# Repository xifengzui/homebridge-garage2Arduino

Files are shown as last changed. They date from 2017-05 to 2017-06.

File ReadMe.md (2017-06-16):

## Arduino Garage Controller base on homebridge 

This project is based on [homebridge](https://github.com/nfarina/homebridge)

this project is a  complete project which aim to use siri to control my  garage.

**It contains**  

**Homebridge plug-ins**: garage controller plugins.

**Sch Pcb** :mother board for DCDC Power module,Arduino Nano V3,ESP8266 wifi module,OLED Screen,Relay module,Rotray Encoder and 3 touch button.(Altium Designer 14.1)

**Model**:   bracket (Sketchup Pro 2015)

Read More: http://www.arkis.me

本项目包含一个完整使用siri控制车库的所有内容。

包含了以下内容

Homebridge插件:转接homebridge命令为socket通讯，控制车库控制器

电路原理图及制版图:主板，用于支持220V转5V电源，3v3电源，Arduino Nano V3,ESP8266无线模块，

OLED屏幕，继电器，旋转编码器及3个触摸按钮

3d模型:可用于3D打印的外壳模型。

具体说明请查看 http://www.arkis.me

**Working Flow**

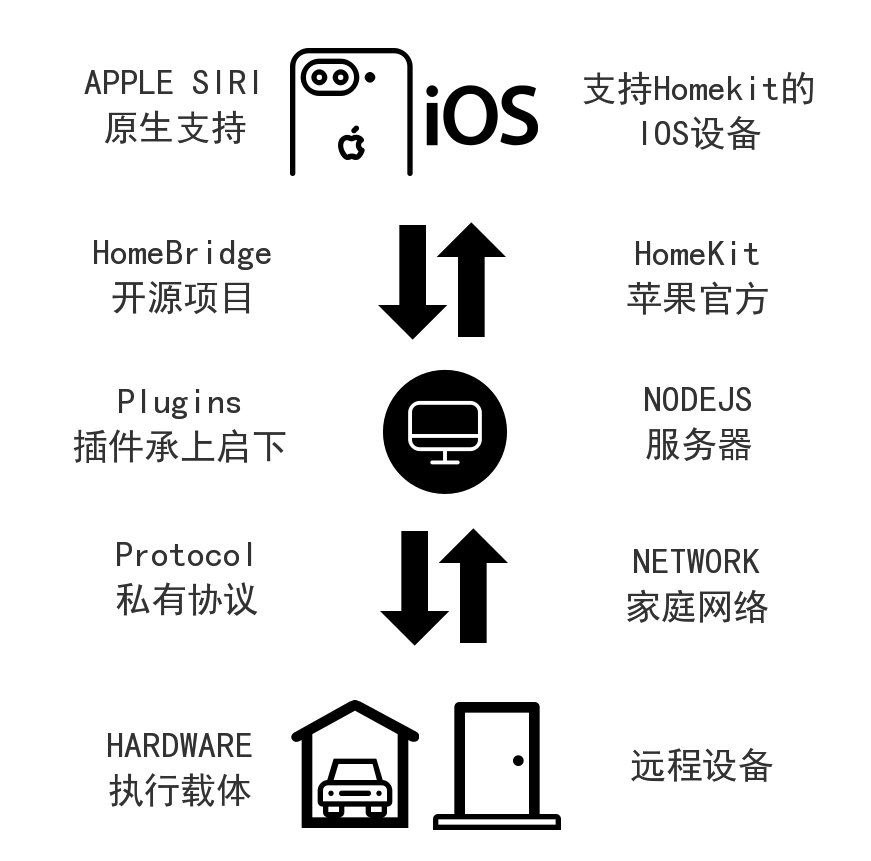
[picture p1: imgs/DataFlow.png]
dataflow


**Network Topology**

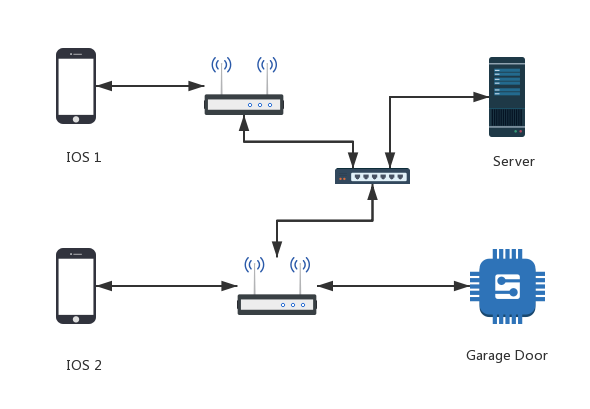
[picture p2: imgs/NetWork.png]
network topology


**Hardware**

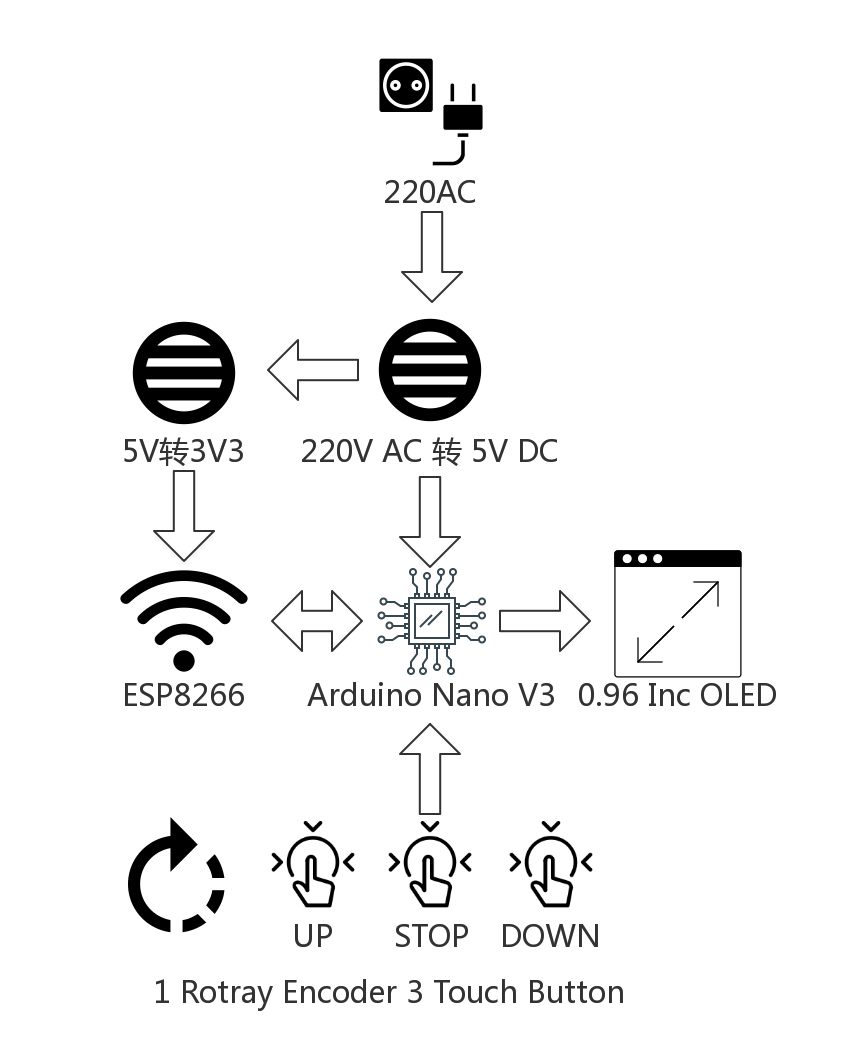
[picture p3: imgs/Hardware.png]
hardware


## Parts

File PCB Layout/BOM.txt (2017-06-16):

名称						价格	数量	用途	TB地址	备注
ESP8266串口WIFI无线模块WIF收发无线模块		9.4	1	数据收发	https://detail.tmall.com/item.htm?id=540067174120&spm=a1z09.2.0.0.xazHRp&_u=v96l7ape468
Arduino Nano V3 ATMega328P			9.2	1	主控	https://item.taobao.com/item.htm?spm=a1z09.2.0.0.xazHRp&id=531487412230&_u=v96l7apf7c1	
4路带继电器光耦模块				6.59	1	电机控制	https://item.taobao.com/item.htm?spm=a1z09.2.0.0.xazHRp&id=6731653313&_u=v96l7ap744f	
220V转5V电源模块				10.5	1	总电源	https://buyertrade.taobao.com/trade/itemlist/list_bought_items.htm?spm=a21bo.50862.1997525045.2.RBEhap	
电源3脚插座					5	1	电源头	https://item.taobao.com/item.htm?spm=a1z09.2.0.0.xazHRp&id=520812099558&_u=v96l7apd51a
电源3脚插母					4.5	1	电源母头	https://item.taobao.com/item.htm?spm=a1z09.2.0.0.xazHRp&id=523912847491&_u=v96l7ap084a	
触摸按钮					2.6	3	按钮	https://detail.tmall.com/item.htm?id=524832982387&spm=a1z09.2.0.0.xazHRp&_u=v96l7ap4716	按钮功能
旋转编码器					5	1	旋钮	https://buyertrade.taobao.com/trade/itemlist/list_bought_items.htm?spm=a21bo.50862.1997525045.2.RBEhap	旋钮
5V转3.3V DCDC电源模块				4	1	3v3电源	https://item.taobao.com/item.htm?spm=a1z09.2.0.0.xazHRp&id=534263863865&_u=v96l7ap15f1	给ESP8266供电
6pin排线					0.6	1	排线	https://item.taobao.com/item.htm?spm=a1z09.2.0.0.xazHRp&id=542126237591&_u=v96l7ap46ef	连接继电器模块的
M3螺丝若干	 	 	 	
OLED Screen                                     14.8    1       显示屏  https://item.taobao.com/item.htm?spm=a1z09.2.0.0.3NjgBQ&id=40854288700&_u=g96l7ap0f8b	 	 
总价	57.3

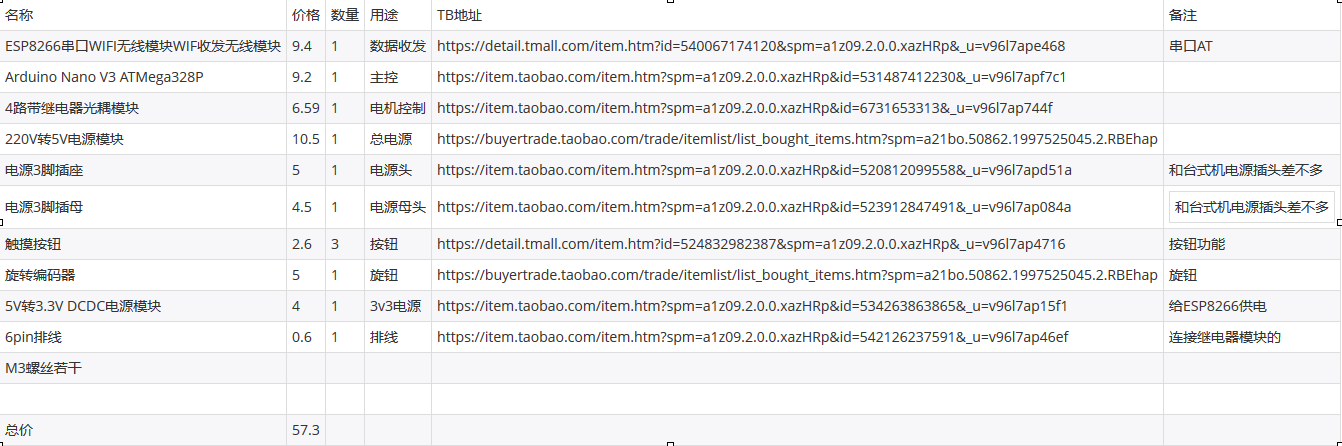
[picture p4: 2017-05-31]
PCB Layout/BOM.png

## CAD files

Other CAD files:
3D Model/box Left.skp
3D Model/box Right.skp
3D Model/box.skp

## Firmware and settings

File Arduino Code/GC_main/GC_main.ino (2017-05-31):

/*****************************************************************************
* File    : GC_main.ino
* Author  : 惜枫醉
* Date    : 2017/04/06
* Brief   : 车库控制器主程序
*
* Copyright (c) 2000-2020 惜枫醉 All Rights Reserved.
* Remarks :修改日志
******************************************************************************/


/*****************************************************************************
*                               头文件引用
******************************************************************************/
//arduino头文件都要包在主文件里，还是比较奇怪的,还有 所有函数都不需要预先声明，但C++部分又是要声明的。
#include <MsTimer2.h>
#include <avr/pgmspace.h>
#include <EEPROM.h>
//#include <Wire.h>
#include "GC_eeprom.h"
#include "GC_def.h"
#include "GC_key.h"
#include "GC_relay.h"
#include "GC_timer.h"
#include "GC_oled.h"
#include "GC_oledFont.h"
#include "GC_menu.h"
#include "GC_wifi.h"
/*****************************************************************************
*                                常量定义
******************************************************************************/


/*****************************************************************************
*                                 宏定义
******************************************************************************/
#define DMSG
#ifdef DMSG
    #define dbgMsg(x) do{\
        char *dbgStr = PSTR(x);\
        while(pgm_read_byte(dbgStr) != NULL)\
        {\
            Serial.write(pgm_read_byte(dbgStr));\
            dbgStr++;\
        }\
        Serial.write('\n');\
    }while(0)
        
#else
    #define dbgMsg(x) 
#endif

/*****************************************************************************
*                              数据类型定义
******************************************************************************/


/*****************************************************************************
*                                函数声明
******************************************************************************/


/*****************************************************************************
*                                变量定义
******************************************************************************/

void setup()
{
    int ret = NULL;
    Serial.begin(9600);
    EEPROM_init();
    TIMER_init();
    OLED_init();
    KEY_init();
	RELAY_init();
    delay(1000);
    WIFI_init();
    APP_menuGen();//生成菜单，如果对菜单逻辑有疑问，可以参考此代码
    
    
}   

void loop() 
{
    APP_menuLogic();
    APP_backgroundService();
    APP_timerServiceBody();
}

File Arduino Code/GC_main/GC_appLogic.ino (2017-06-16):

/*****************************************************************************
* File    : GC_appLogic.ino
* Author  : 惜枫醉
* Date    : 2017/04/09
* Brief   : 车库控制的总逻辑 
*
* Copyright (c) 2000-2020 惜枫醉 All Rights Reserved.
* Remarks :修改日志
******************************************************************************/


/*****************************************************************************
*                               头文件引用
******************************************************************************/


/*****************************************************************************
*                                常量定义
******************************************************************************/


/*****************************************************************************
*                                 宏定义
******************************************************************************/
#define TEXT_ALIGN_LEFT     0
#define TEXT_ALIGN_MIDDLE   1
#define TEXT_ALIGN_RIGHT    2

#define GARAGE_TIME_UP      0
#define GARAGE_TIME_DOWN    1

#define WIFI_MAX_NAME_LEN 16
#define WIFI_MAX_PASSWD_LEN 16


#define STAT_SELECT_CHAR 0
#define STAT_EDIT_CHAR 1
#define STAT_STRLEN_CHANGE 2



#define STAT_HK_CLOSED  0   //已关闭
#define STAT_HK_CLOSING 1   //关闭中
#define STAT_HK_CLOSE   2   //请求关闭

#define STAT_HK_OPENED  3   //已打开
#define STAT_HK_OPENING 4   //打开中
#define STAT_HK_OPEN    5   //请求打开

#define STAT_HK_IDEL 6
#define STAT_HK_BUSY 7

/*****************************************************************************
*                              数据类型定义
******************************************************************************/
struct APP_GarageParms
{
    Uint8 upTime;
    Uint8 *upTimeStr;
    Uint8 downTime;
    Uint8 *downTimeStr;
    volatile Uint8 isEnableHomeKit;
    volatile Uint8 status;
};

struct APP_WifiParms
{
    Uint8 isConnected;
    Uint8 *ssid;
    Uint8 ssidLen;
    Uint8 *password;
    Uint8 passwordLen;
    Uint8 *srvIp;
    Uint8 devId;
};


struct APP_serviceParms
{
    Uint8 *wifiStatus;
};

/*****************************************************************************
*                                函数声明
******************************************************************************/


/*****************************************************************************
*                                变量定义
******************************************************************************/


//主页菜单项  
static MENU_Handle      gMainMenu = NULL; 
static MENU_ItemHandle  gMainMenu_garage = NULL;
static MENU_ItemHandle  gMainMenu_wifi = NULL;

//车库菜单项
static MENU_Handle      gGarageMenu = NULL;
static MENU_ItemHandle  gGarageMenu_goBack = NULL;
static MENU_ItemHandle  gGarageMenu_upTimeMenu = NULL;
static MENU_ItemHandle  gGarageMenu_downTimeMenu = NULL;
static MENU_ItemHandle  gGarageMenu_enableHomekit = NULL;
static MENU_ItemHandle  gGarageMenu_disableHomekit = NULL;

//wifi菜单项
static MENU_Handle      gWifiMenu = NULL;
static MENU_ItemHandle  gWifiMenu_goBack = NULL;
static MENU_ItemHandle  gWifiMenu_ssid = NULL;
static MENU_ItemHandle  gWifiMenu_password = NULL;
static MENU_ItemHandle  gWifiMenu_connect = NULL;
static MENU_ItemHandle  gWifiMenu_srvIp = NULL;
static MENU_ItemHandle  gWifiMenu_devId = NULL;

//索引句柄，整个菜单的渲染逻辑通过索引句柄来进行的
static MENU_Handle *posHandle = NULL;
static MENU_ItemHandle *posItemHandle = NULL;

//服务器IP地址,设备会向这个ip上报车库门的状态 
static Uint8            gSrv_ip[4] = {192,168,1,200};

//车库门上和下的时间设置
static Uint8            gGarageMenu_downTimeDispMem[] =    "DOWN TIME: 15";
static Uint8            gGarageMenu_upTimeDispMem[]   =    "UP   TIME: 15";

//wifi字符串的内存
static Uint8            gWifiMenu_wifiNameMem[WIFI_MAX_NAME_LEN+1] = "";
static Uint8            gWifiMenu_passwordMem[WIFI_MAX_PASSWD_LEN+1] = "";


static volatile Uint8 gTimerDaemonFlag = 0;//由于定时器中断不建议做很多事情，所以用标志位，让她在主函数运行


static volatile Uint16 gClock = 0; //用于整个设备的计数时间戳

struct APP_GarageParms gAPP_garagePrms = 
{
    .upTime = 0,
    .upTimeStr = gGarageMenu_upTimeDispMem,
    .downTime = 0,
    .downTimeStr = gGarageMenu_downTimeDispMem,
    .isEnableHomeKit = 0,
    .status = STAT_HK_IDEL
};

struct APP_WifiParms gApp_wifiPrms = 
{
    .isConnected = 0,
    .ssid = gWifiMenu_wifiNameMem,
    .ssidLen = 4,
    .password = gWifiMenu_passwordMem,
    .passwordLen = 8,
    .srvIp = gSrv_ip,
    .devId = 66
};


/*****************************************************************************
* Author  : 惜枫醉
* Date    : 2017/05/28
* Brief   : 从eeprom获取掉电的数据
* Return  : 
* Remarks : 
******************************************************************************/
Uint8 APP_dumpPrms(void)
{
    gAPP_garagePrms.upTime =  EEPROM_restore(EEPROM_UPTIME);
    gAPP_garagePrms.downTime =  EEPROM_restore(EEPROM_DOWNTIME);
    gApp_wifiPrms.srvIp[0] = EEPROM_restore(EEPROM_SRVIPSEG0);
    gApp_wifiPrms.srvIp[1] = EEPROM_restore(EEPROM_SRVIPSEG1);
    gApp_wifiPrms.srvIp[2] = EEPROM_restore(EEPROM_SRVIPSEG2);
    gApp_wifiPrms.srvIp[3] = EEPROM_restore(EEPROM_SRVIPSEG3);
    gApp_wifiPrms.devId = EEPROM_restore(EEPROM_DEVID);
    gAPP_garagePrms.isEnableHomeKit = EEPROM_restore(EEPROM_ISENHOMEKIT);
}
/*****************************************************************************
* Author  : 惜枫醉
* Date    : 2017/05/28
* Brief   : 将数据刷入eeprom
* Return  : 
* Remarks : 
******************************************************************************/
Uint8 APP_flushPrms(void)
{
    if(gAPP_garagePrms.upTime !=  EEPROM_restore(EEPROM_UPTIME))
    {
        EEPROM_store(EEPROM_UPTIME, gAPP_garagePrms.upTime);
    }
    
    if(gAPP_garagePrms.downTime !=  EEPROM_restore(EEPROM_DOWNTIME))
    {
        EEPROM_store(EEPROM_DOWNTIME, gAPP_garagePrms.downTime);
    }

    if(gApp_wifiPrms.srvIp[0] !=  EEPROM_restore(EEPROM_SRVIPSEG0))
    {
        EEPROM_store(EEPROM_SRVIPSEG0, gApp_wifiPrms.srvIp[0]);
    }

    if(gApp_wifiPrms.srvIp[1] !=  EEPROM_restore(EEPROM_SRVIPSEG1))
    {
        EEPROM_store(EEPROM_SRVIPSEG1, gApp_wifiPrms.srvIp[1]);
    }

    if(gApp_wifiPrms.srvIp[2] !=  EEPROM_restore(EEPROM_SRVIPSEG2))
    {
        EEPROM_store(EEPROM_SRVIPSEG2, gApp_wifiPrms.srvIp[2]);
    }

    if(gApp_wifiPrms.srvIp[3] !=  EEPROM_restore(EEPROM_SRVIPSEG3))
    {
        EEPROM_store(EEPROM_SRVIPSEG3, gApp_wifiPrms.srvIp[3]);
    }
    
    if(gApp_wifiPrms.devId !=  EEPROM_restore(EEPROM_DEVID))
    {
        EEPROM_store(EEPROM_DEVID, gApp_wifiPrms.devId);
    }

    if(gAPP_garagePrms.isEnableHomeKit != EEPROM_restore(EEPROM_ISENHOMEKIT))
    {
        EEPROM_store(EEPROM_ISENHOMEKIT, gAPP_garagePrms.isEnableHomeKit);
    }
}
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

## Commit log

2017-05-31 create project
    [box Left.skp, box Right.skp, box.skp]
2017-06-16 fix connection issue. The WIFI module might work in unknow stat,when this situation happend,Arduino will disconnect, wait for sometime ,and then ,reconnect to the server.
    [GC_appLogic.ino, GC_key.ino]
2017-06-16 update working flow topology and hardware specification.
2017-06-16 The device will reconnect to the server when restart.The connection stat will be store in EEPROM.
2017-06-16 add OLED BOM Info
